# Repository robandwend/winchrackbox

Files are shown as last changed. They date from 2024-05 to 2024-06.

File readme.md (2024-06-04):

# WinchRack-Box V1.1 (WRB)
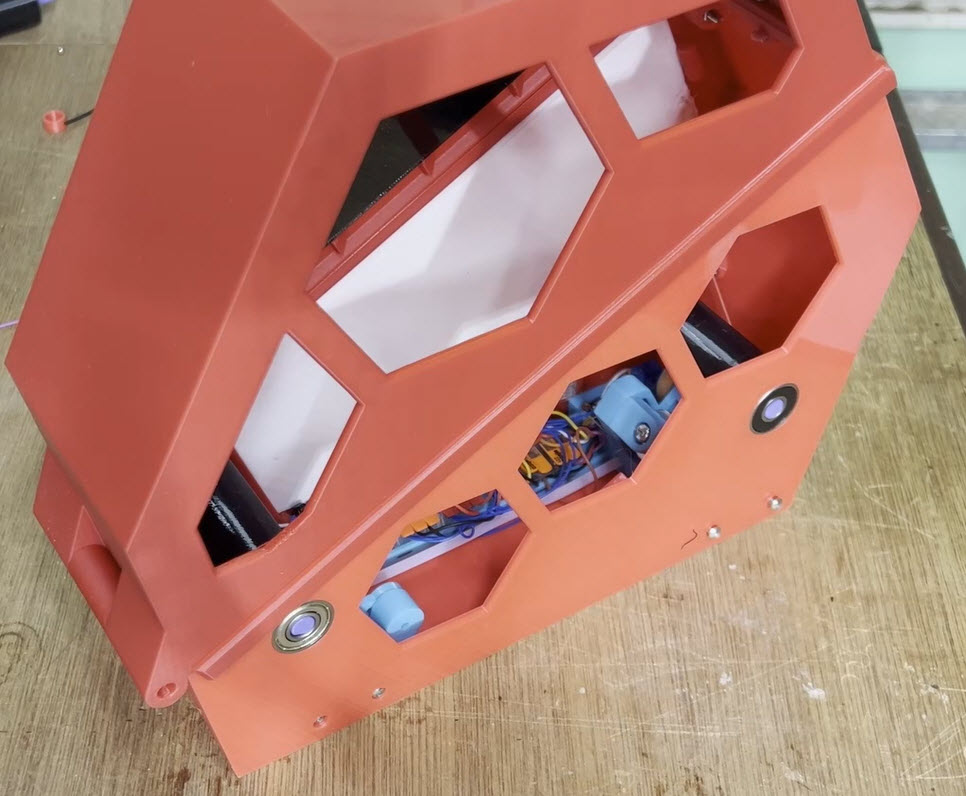
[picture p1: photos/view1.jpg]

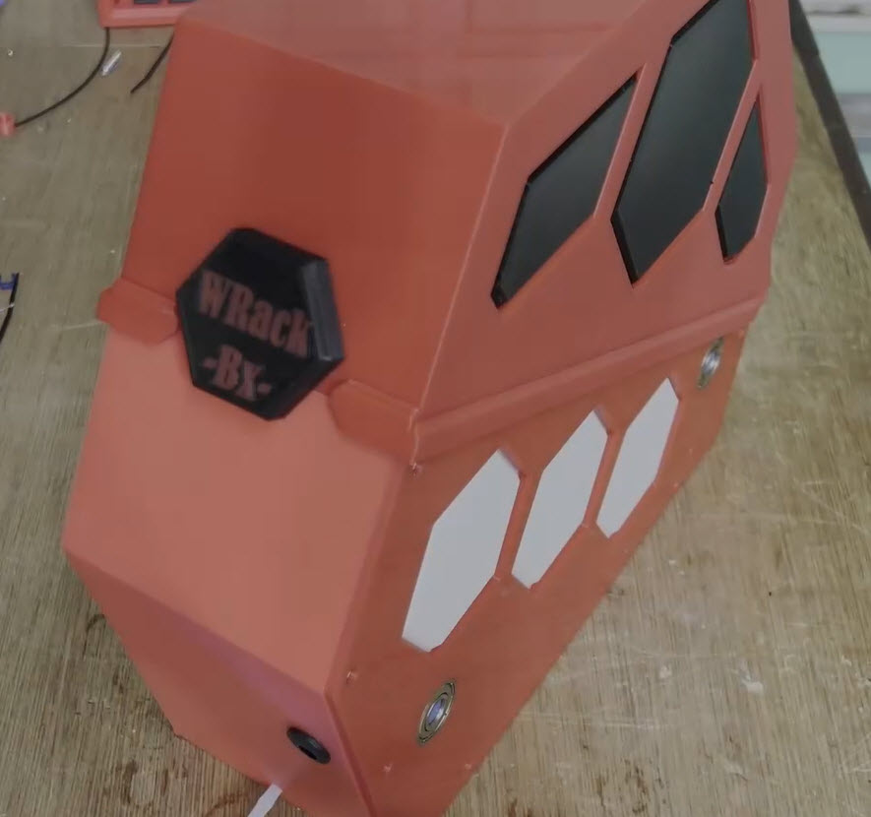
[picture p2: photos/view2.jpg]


## About

Multi filament printers such as ERCF & MMU require some way to store the filament that is retracted during a filament swap.
Various 'buffer' implementations exist for this purpose, however they occupy much space, and make loading / unloading filament more difficult.

The AMS implementation is much neater, rewinding the filament automatically back onto the spool.

This box design allows the spool to be neatly stored, with no need for 'buffers' when used in filament swappers.

The rewind mechanism inside the box is based on this original design by 'Mr Goodman' [LINK TO ORIGINAL WINCHRACK](https://github.com/pure100kim/WinchRack_Type2/tree/main). Although I did made a number of small changes to this design (see [MY CHANGES](https://www.printables.com/model/840978-winchrack_type2-filament-rewinder-for-ercf) ) which I would recommend for the WRB.

The mechanism now has both rollers motor driven to improve the functioning with light (near empty) filament rolls.

The BOM below however is a full component list for the box and mechanism.

Total cost of building a WRB excluding plastics should be less than $17US (plus any shipping costs).

## Youtube intro video

https://youtu.be/9757P2IB9eM

## Printables

https://www.printables.com/model/897767-winchrack-box

## BOM 

Wago 5pin x 2

- Opto endstop x 1 (https://www.aliexpress.com/item/1005005304758202.html)
- n20 gear motor 300 rpm 5v ~ 6v x 1 (https://www.aliexpress.com/item/32910935772.html)
- Solenoid 5v/3kg x 2 (https://www.aliexpress.com/item/32575060483.html)
- mosfet switch 1ch x 1 (https://www.aliexpress.com/item/1005006165294338.html)
- 608zz Bearings x 4 (https://www.aliexpress.com/item/1005005321486587.html)
- 623zz Bearings x 8 (https://www.aliexpress.com/item/1005005480256021.html)
- silicon ring x 1 (https://www.aliexpress.com/item/1005005445878990.html)
- PTFE tube 3x4 or 2x4 (https://www.aliexpress.com/item/1005001408141263.html)
- m3 insert nut (OD 5mm, L 4mm)
- m3 bolts (get a selection pack if you've not already got one)
- m2 self tapping screw 8~10mm x 4
- 6mm collet for 4mm PTFE Tube x 1 (https://www.aliexpress.com/item/4001119588533.html)
- D2F Micro switch (https://www.aliexpress.com/item/1005004693669754.html)
- 4mm Bearing ball (https://www.aliexpress.com/item/1005003377385833.html) (Or these can be taken from inside a 608zz bearing)
- 12V 3A DC Power Connector (https://www.aliexpress.com/item/1005005610836339.html)
- Assorted wego style connectors (https://www.aliexpress.com/item/1005007090402568.html)
- 5V power supply (plugged for your country)

## HOLE VERSION

NOTE: A version of the top hat is available with an additional hex hole in the top (handy if they are all stacked next to each other). 

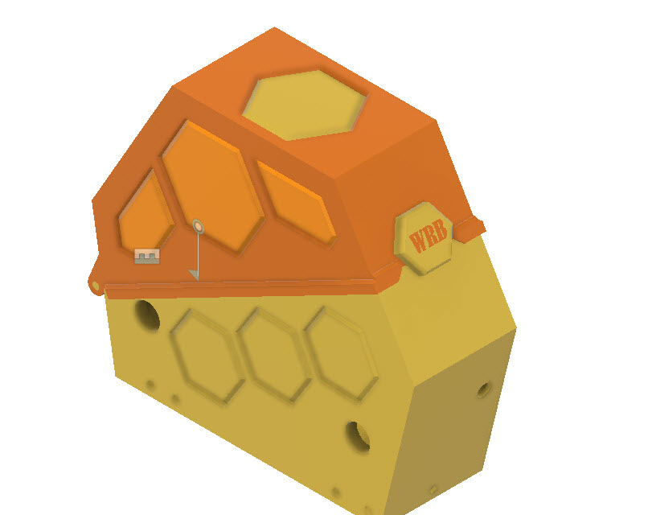
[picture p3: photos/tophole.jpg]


## PRINTING

I've printed all parts in both PLA and PETG and haven't had any problems with either.

### Size

The largest component is the base box, which requires a bedsize of 256x256. I printed on an X1C and a Voron2.4.

### Supports

- The bufferbase_mount (support under the solenoid mount). 

- The box-top as indicated below:

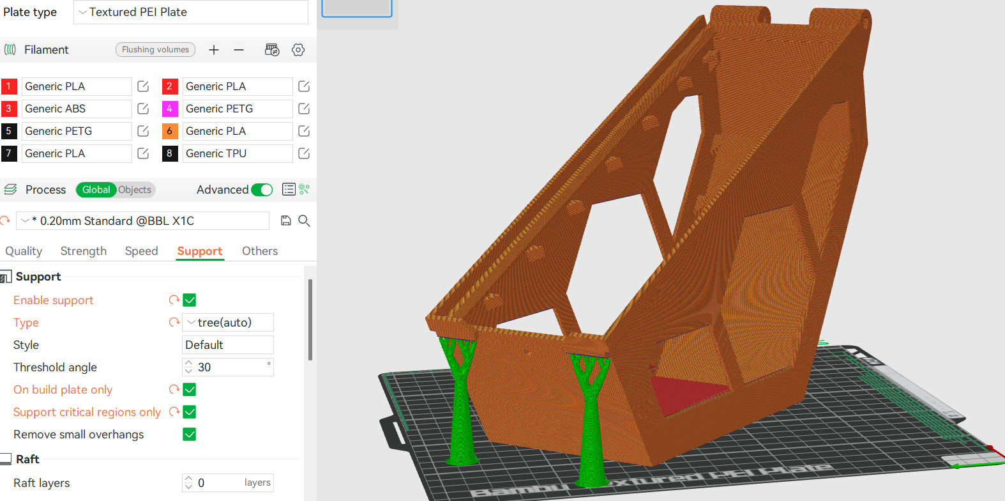
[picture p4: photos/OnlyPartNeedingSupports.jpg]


### Sensor key colour

The opticalsensorkey should be printed in a dark colour to avoid light affecting the optical sensor.

### Rollers

I suggest printing the rollers in TPU to increase friction.

### Sizing

If you find the rollers are not fully connecting to the drive wheels when rewinding, you may wish to reprint the rollers slightly scaled in circumference (say 1mm). I found I needed to do this with one brand of TPU due to shrinkage during printing.

### Knob

The knob is provided as an stl with two bodies, which can be split in the slicer to print the text in a different colour. If the text is not required, then don't split the stl.

Alternatively the knob-no-text stl can be printed, this has the text indented into the knob (ie a single colour print with the text indented).

## BUILD GUIDE

Let the fun begin.

A number of part will need heatset inserts, I'll highlight these as we go.

### Prefer 12Volts?

This is currently a 5Volt build. However by replacing the motors with 12Volt ones, every other component will then work on 12V if preferred.

### Use the right base plate

My suggestion is to build the mechanism onto the right base plate, and get the electronics working before fully assembling the box. I've used wego style connectors to simplify much of the connections. These also allow easy changes to motor directions etc if needed. The wego boxes should snap into place as indicated.

### Insert panels

The hexagonal holes in the box frame are filled with the four panels. Alternatively they can be replaced by 3mm thick clear sheeting cut to size (print a panel as a cutting guide). The panel click into place - however you may want to place a bead of CA glue around their edges to strengthen and reduce air flow.

If you have printed the top with a additional hex hole on its top, then the additional top panel will also be needed (or a clear 3mm perspex cut to size). Note that this panel is a very tight fit, and may require the edges trimmed slightly to fit.

### Drive mechanism

The drive mechanism consists of two separate units, the front and the rear. Both have a drive motor, the rear also has the filament movement sensor.

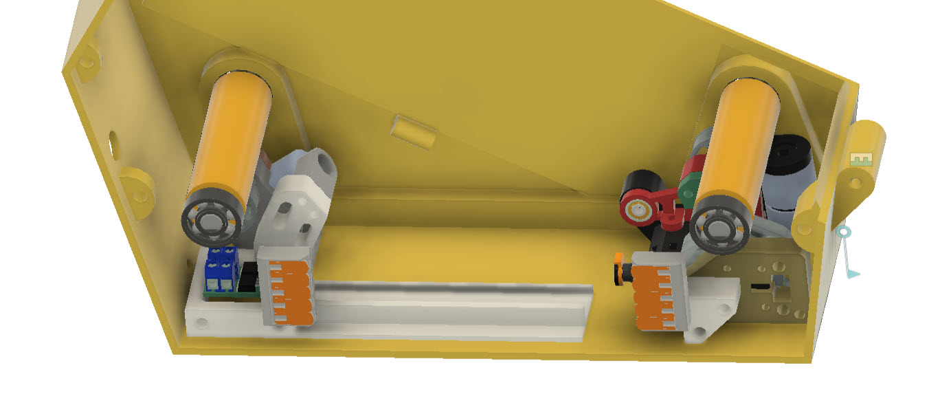
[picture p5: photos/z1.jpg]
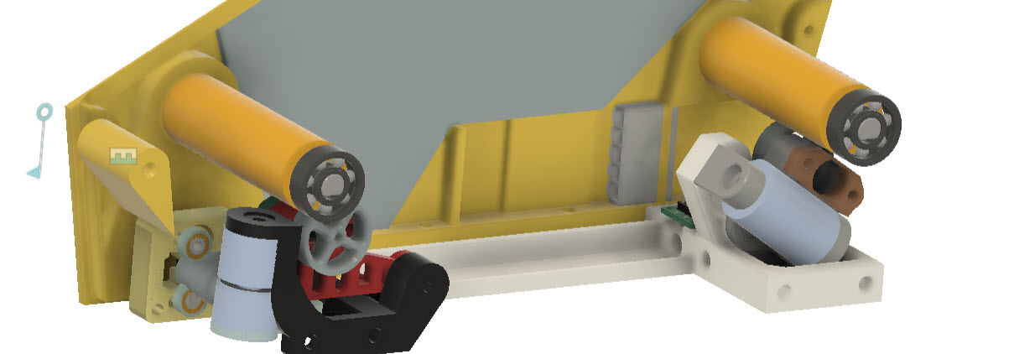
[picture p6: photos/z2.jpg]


## FRONT ASSEMBLY

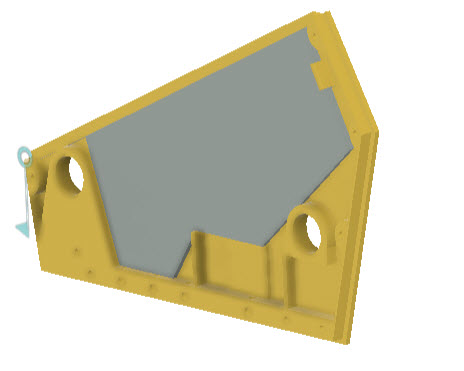
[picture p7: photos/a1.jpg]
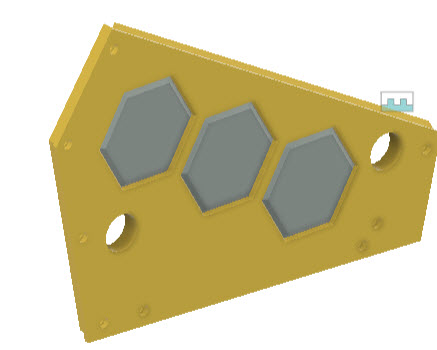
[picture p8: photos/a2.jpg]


- Insert the 608 bearings into the left and right bodies.
- Clip in two 5-point wego connectors
- Clip in the right panel (you can leave out for later if you prefer, this is removable even when completed.)
- Select all the printed parts for the front-assembly.

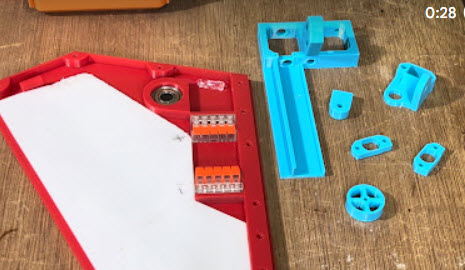
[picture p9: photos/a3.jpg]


- Insert heatset inserts into the locations indicated below

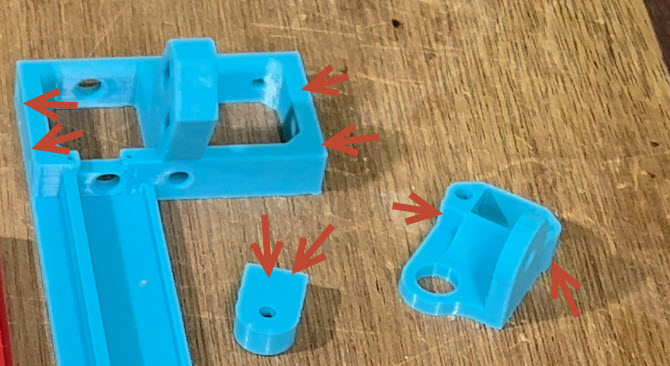
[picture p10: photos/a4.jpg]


- Put the small rubber band around the drive wheel. I find using a small allen key helps lever the band into place.
- Push a small bearing into the AcceleratorMount.
- Assemble the motor into AcceleratorMount and mount cover, and push on the drive wheel.
  - Note that the rear motormount has a small cut-away area that the front one does not have.
  - The wheel must align to the notch on the motor shaft. The fit can be very tight - fortunately the motors can take a surprising amount of pressure.
- Solder a length of wire to the motor (its not clear which is +ve/-ve so later we will test the direction).
  - I always used longer wire leads than needed to ensure I could cut to length later.

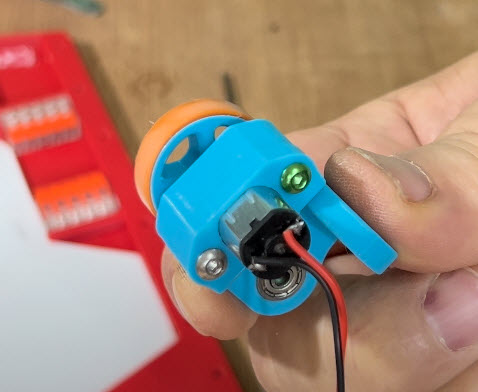
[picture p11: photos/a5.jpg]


- The accelerator assembly will then pivot on the front-base-accel-pedal-mount using the inserted bearing. Screw an m3 bold through the bearing into the pedal-mount.
  - Note that the assembly should move freely as indicated.

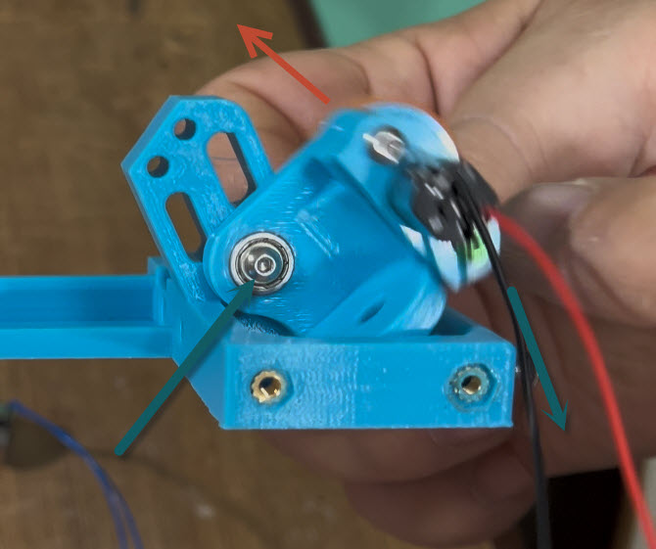
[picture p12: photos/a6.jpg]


Insert a screw into the rear of the mount as shown below. This screw can be used to restrict how far the assembly drops (we only needs about 2mm gap between the solenoids once fitted).

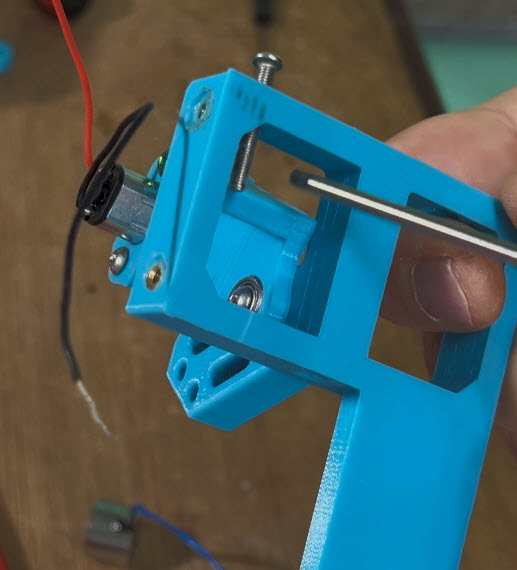
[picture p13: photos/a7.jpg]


- Attach a solenoid as shown using an m4 bolt (sometimes the bolt is supplied with the solenoid - sometimes its not).
- Route the four wires through the base, using the 2nd hole (the first/middle hole is for ptfe tube for the filament to route through).

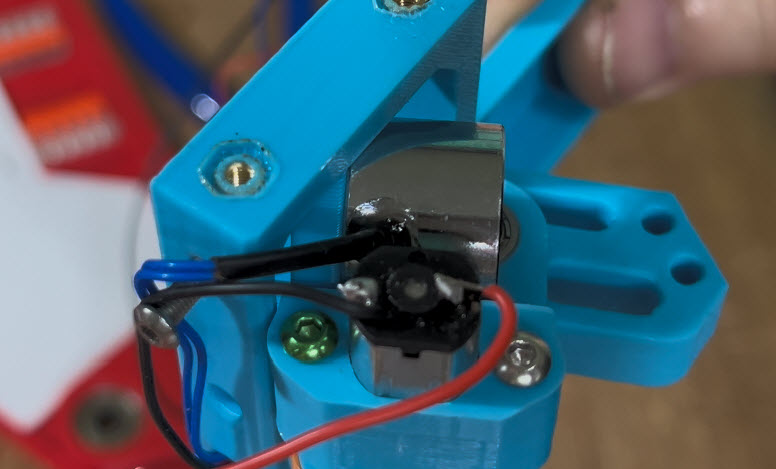
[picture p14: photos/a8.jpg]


- Attach 2nd solenoid to the AccelPedalMagSol

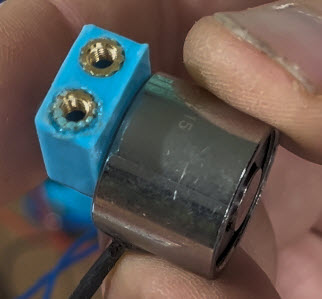
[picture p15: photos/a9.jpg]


- Use two screws to attach this as shown, routing the wires through the slot.

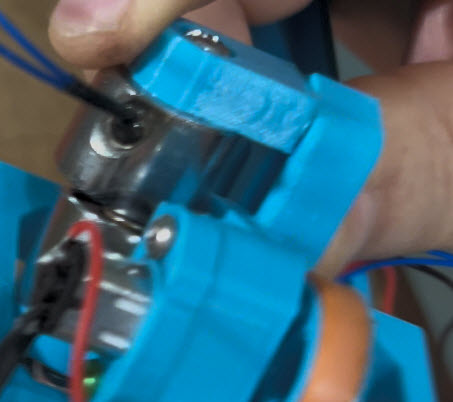
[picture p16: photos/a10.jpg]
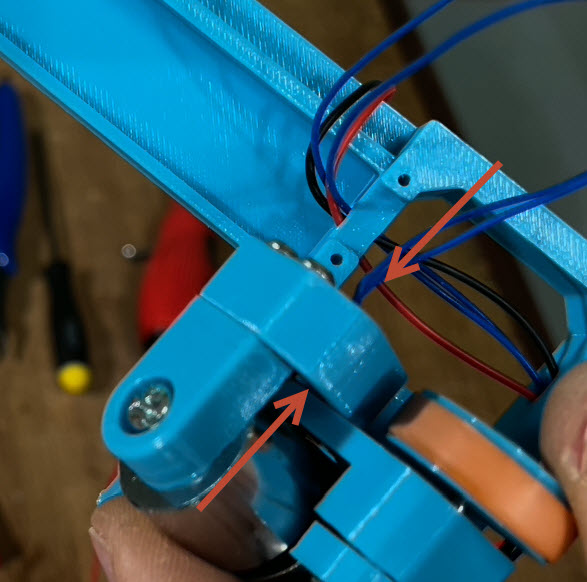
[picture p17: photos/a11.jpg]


- Adjust the solenoids to be flat to each other
  - The screws holding the solenoids and the AccelPedalMagSol all have a very slight movement. Slacken the screws, physically hold the solenoids together, and re-tighten.
  - At this point we are looking for a movement of about 2mm between the solenoids. When held flat on the table, the solenoids should fall apart 2mm easily. The gap can be reduced using the screw inserted at the rear of the base.
  - If the movement is not very easy, then loosen the bolt holding the pivot bearing.
  - Also ensure that the wire routing is not affecting the movement.

<video width="320" height="240" controls>
  <source src="videos/ss.mov" type="video/mp4">
</video>

[You Tube Copy](https://youtu.be/2NZAOF3inoc)

- Take the mosfet switch and connect a length of wire to one of the trigger connections (it doesn't matter which one).
  - Leave a good length of wire as this will route through to the microswitch on the rear assembly.

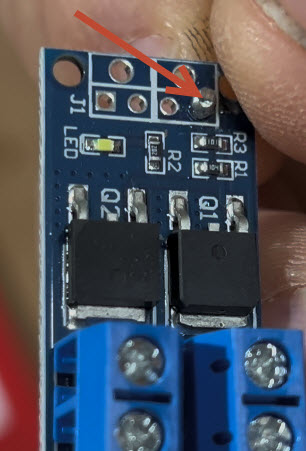
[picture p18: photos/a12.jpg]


- Screw in four lengths of cable to the mosfet as shown. We do this now because once attached to the base, it becomes difficult to a access. Again leave plenty of length on the cables so we can trim to size later.

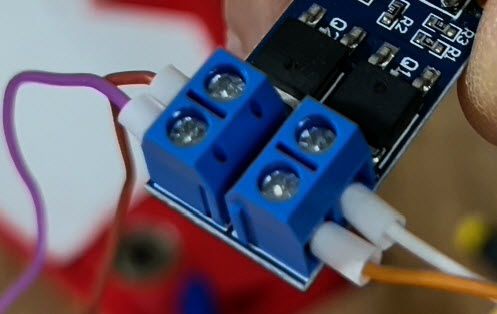
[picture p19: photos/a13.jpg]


- Attach the mosfet to the base as shown using two m2 self-tapping screws.

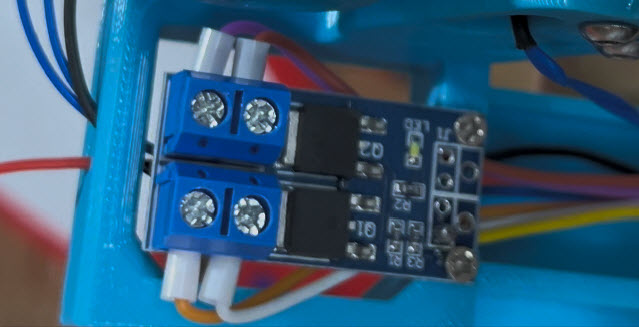
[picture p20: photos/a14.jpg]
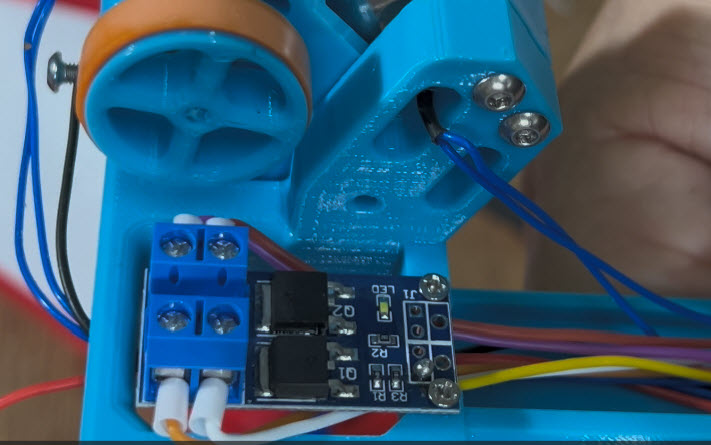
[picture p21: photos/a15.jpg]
 

- Attach the assembly to the side panel using two m3 screws.

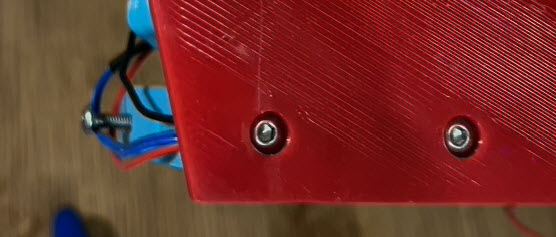
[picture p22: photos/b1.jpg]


### Wiring

For reference here's the wiring design for the original Type2 winchrack, the only change is to add a second motor and set of solenoids. I've added a few extra Wago blocks to aid connections.

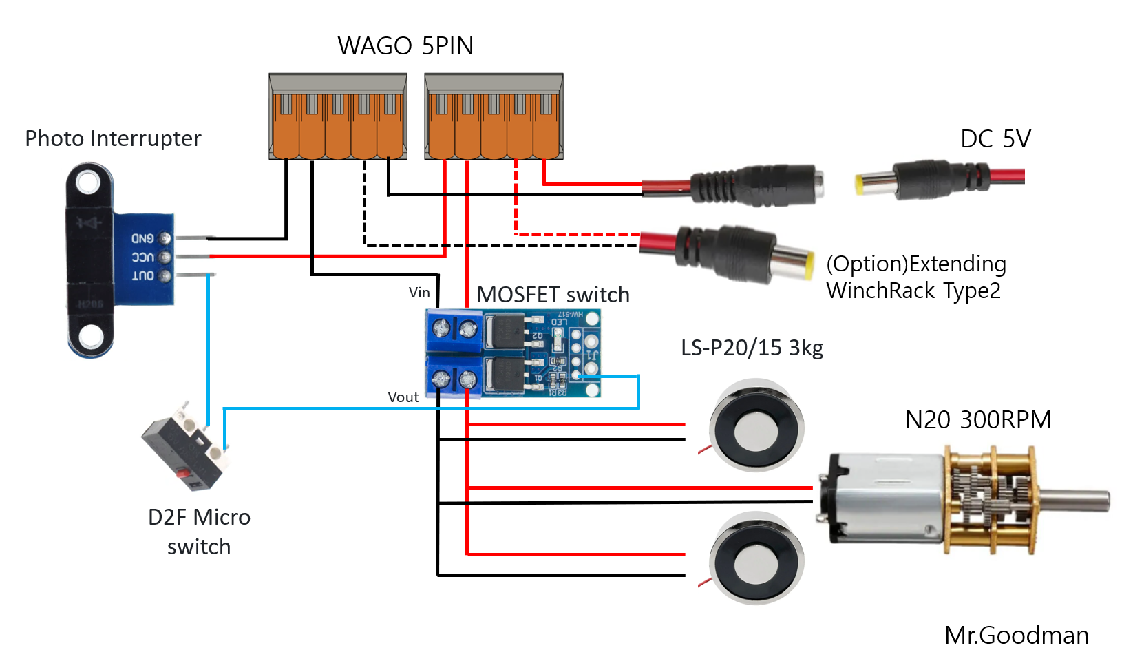
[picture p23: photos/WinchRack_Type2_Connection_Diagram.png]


### Wiring the front assembly

<video width="320" height="240" controls>
  <source src="vidoes/fa.mov" type="video/mp4">
</video>

[You Tube Copy](https://youtu.be/1QWAKU8oQXM)

The front assembly has three devices that need to be driven - The motor, and the two solenoids.

We will use the two wego connectors to create a +ve and -ve terminal, use a marker to indicate which is going to be used for which.

#### Motor connection
  - Use a 5 Volt supply to test the direction of the motor. You want the motor to turn so the top moves to the front of the unit. Shorten and insert the +ve/-ve of the motor into the correct wego blocks.

#### Solenoid connection. 
  - Here we need to determine the correct leads to connect together.
  - Twist one lead from each of the solenoids to one from the other solenoid. Do the same with the 2nd lead from each. 
  - Connect 5V to see if the solenoids snap together (move them by hand to check the distance isn't too far.)
  - If they snap together, then we have the correct pairing, if not, then swap over the pairings and retry.
  - Having established which wires go together, plug the twisted wires into the +ve and -ve wego blocks. (Which is +/-ve doesn't matter),

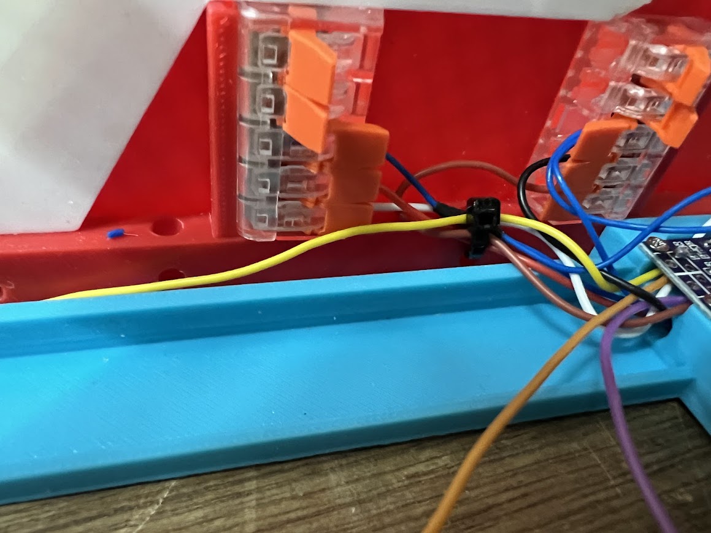
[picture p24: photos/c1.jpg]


- Power in connector block
  - Add to 3-block wego connectors onto the right of the rail on the base of the front assembly. 
  - These will be the main 5V input power points of the build. (The 5-unit blocks are only energised when the motors are to run).
  - Mark the 3-block wego's with +ve and -ve
  - Run a wire from each block back through the hole in the front assembly (where most of the wires are running) - this will later be connected to the power source using a 12v connector. I'd suggest using red/black wires to indicate +/-ve.

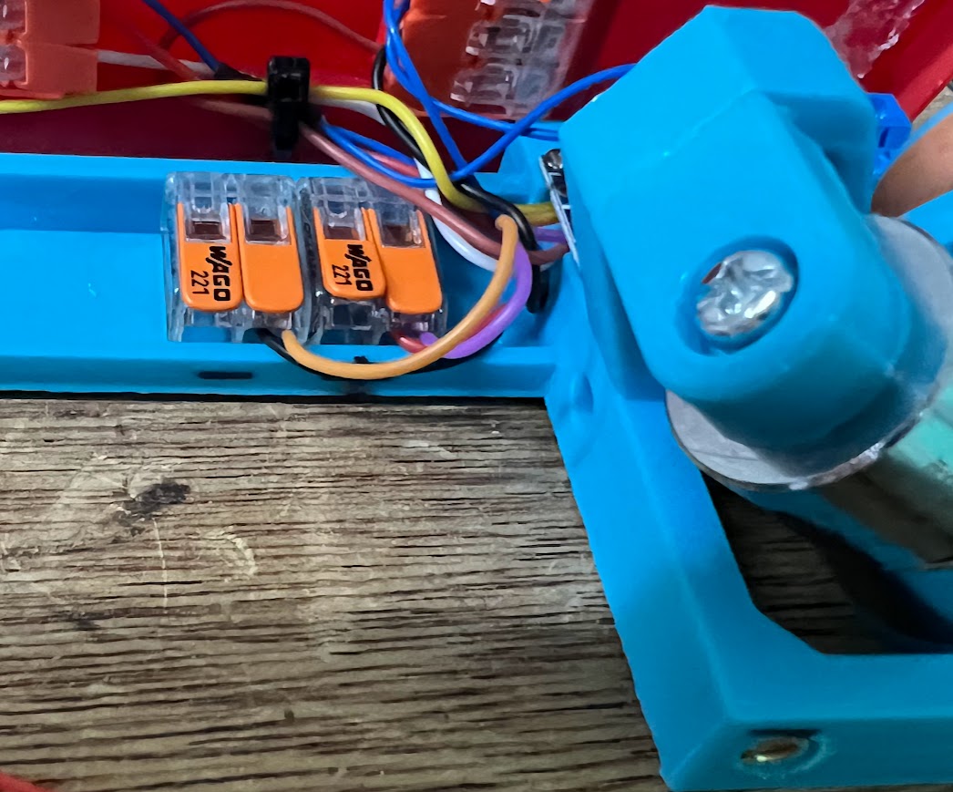
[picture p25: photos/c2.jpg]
 (Note: I've used a 2-connector as this was all I had at hand)
  
- Mosfet connection.
  - Plug the +/-ve IN wires from the mosfet into the +/- 3-block wego connectors (ie the power in wego just added).
  - Plug the +/-ve OUT wires from the mosfet into the +/- 5-block wego connectors (ie to power the motor and the solenoids).
  
At this point the only wire not connected (other than the main 5v power input) is the wire going to the mosfet trigger. This will be connected later.

Note the zip tie connection points down the side to aid tidying the wires.

## REAR Assembly

Gather the parts needed for the rear assembly

- Add heatset inserts as indicated.

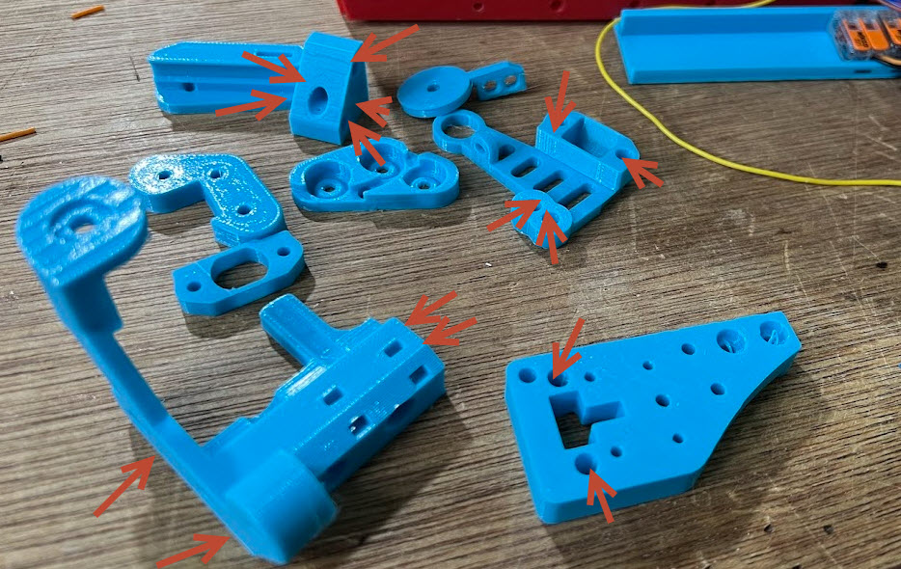
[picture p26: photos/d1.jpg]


### BufferRail Assembly

- Add four bearings as shown. Connected with m3 screws. Ensure they are tight, but free to move.

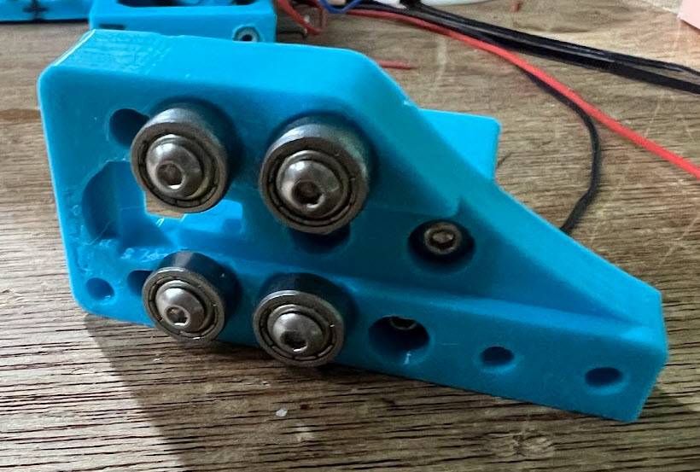
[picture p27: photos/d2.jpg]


- Attach the SensorDetection_sensor_basemount to the bufferrail. Not that this has a hole for later routing of wires.

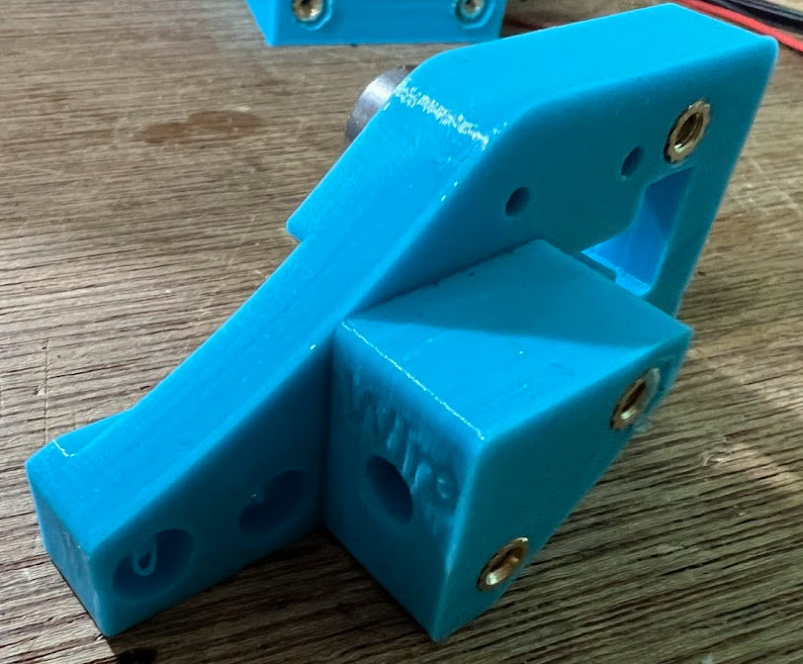
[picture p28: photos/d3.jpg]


- Push a bearing into the AccelPedalMag
- Attach the BaseSolJoint to the AccelPedalMag
- Screw an M3 screw in as shown. This can be used later to restrict the movement of the pedal.
- Solder two wires to the motor (leave sufficient length to trim later).
- Insert the motor into the pedal as shown.

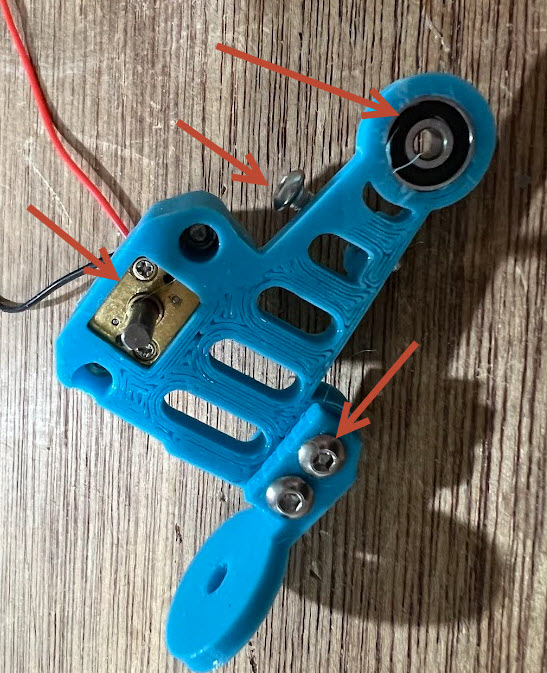
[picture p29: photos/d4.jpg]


- Attach the motor using the motor-mount. Note that the rear motor-mount has a small cut-away area that the front one does not have.

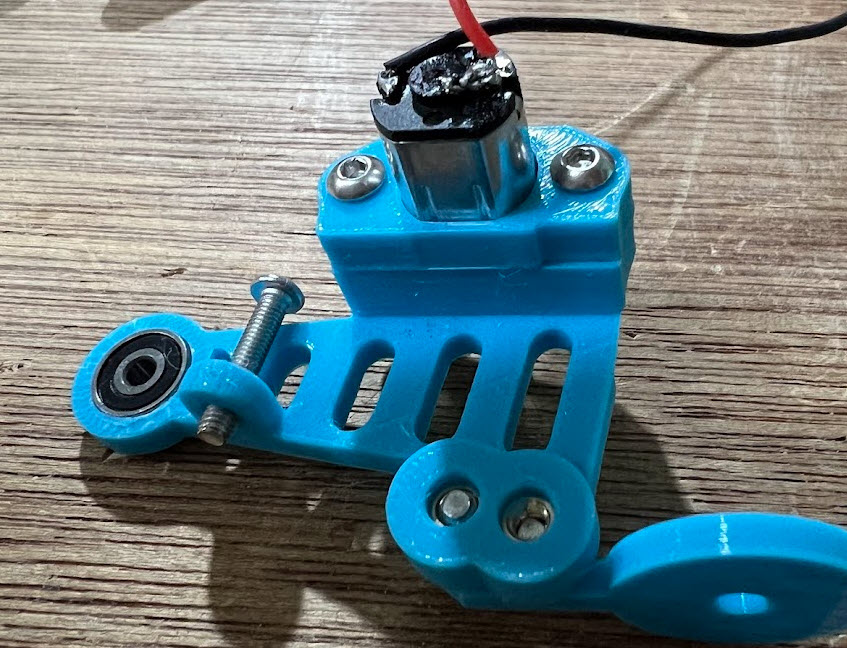
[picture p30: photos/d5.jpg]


- Again place a band over/around the wheel.
- Attach the wheel to the motor, like the front wheel, this is a tight fit.

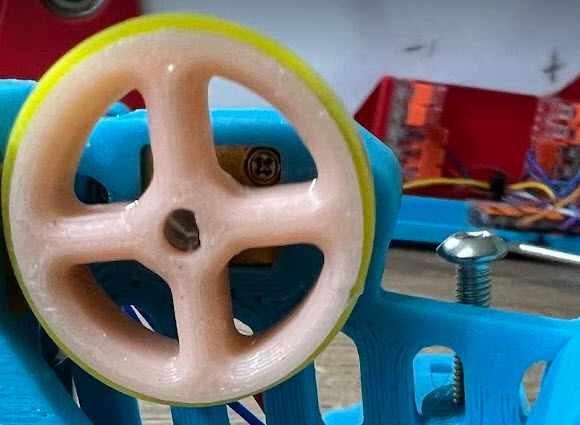
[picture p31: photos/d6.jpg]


- Attach the AccelPedalMag to the Bufferbase_mount with a single screw through the bearing (as done with the front). You can now see how the screw fitted earlier can be used to limit travel.
    - Ensure the pedal moves freely.
    - Ensure your heatset insert isn't as poorly fitted as the one in this photo :-)

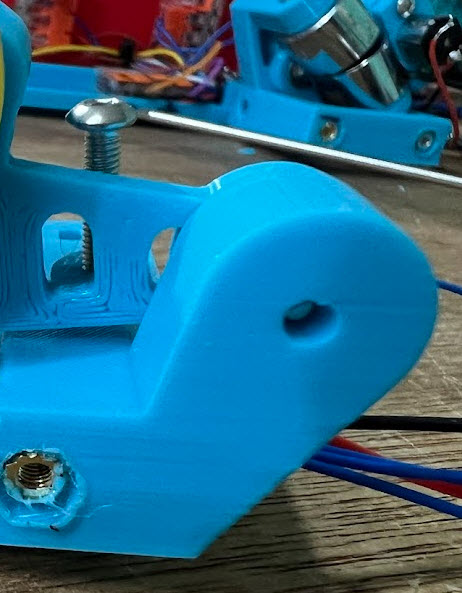
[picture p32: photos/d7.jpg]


### Solenoids

- Attach the solenoids as show.
    - Again use the slight free-play when the screws are loose to ensure a good closed fit between the two solenoids.
    - You only need a 1 or 2mm gap between the open solenoids.

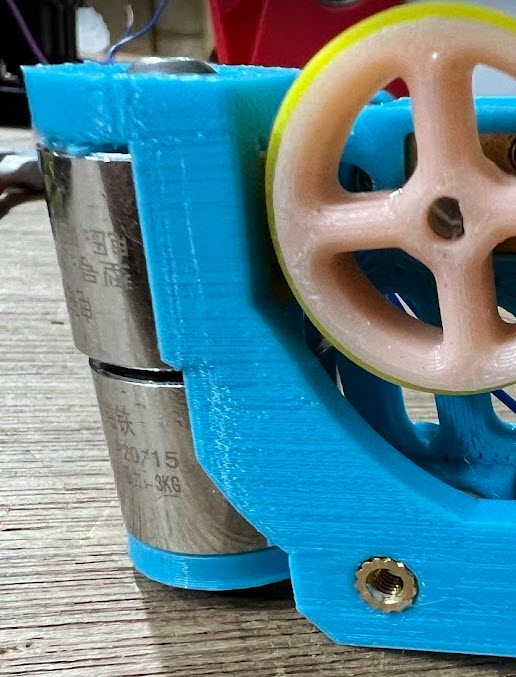
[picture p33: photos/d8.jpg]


- Route the wires through the hole as shown

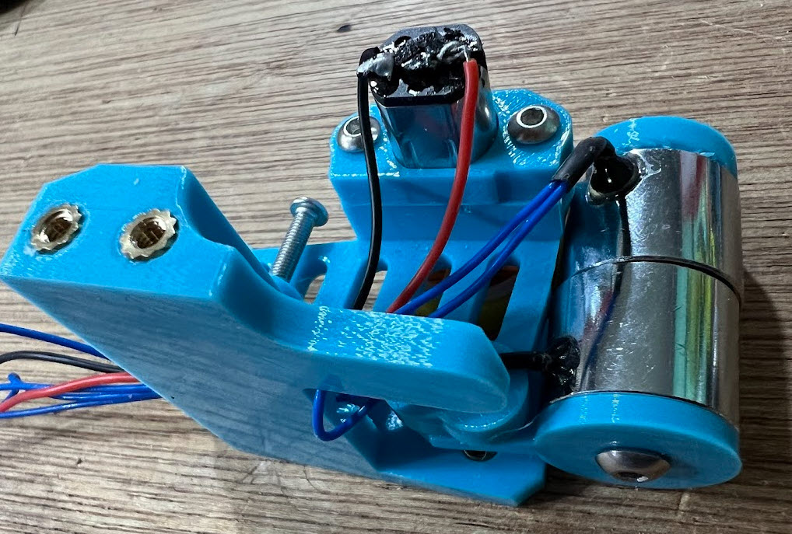
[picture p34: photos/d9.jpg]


### Sensor Roller Assembly

The sensor roller is use to detect filament movement. The filament routes through it between three bearings, the bearings cause a small amount of friction on the filament - thus making the sensor move.

- This image shows the three components of the roller, in order of stacking with the bearings in position.
- Assemble as shown and screw together with three m3 screws.

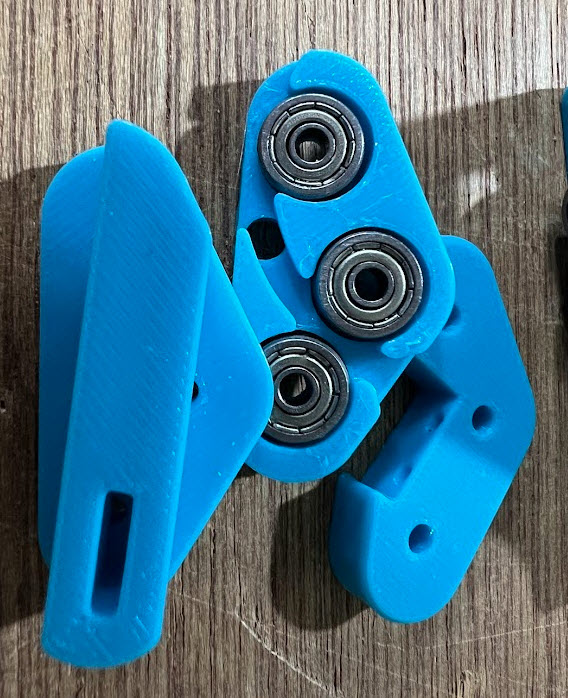
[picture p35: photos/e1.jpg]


- Place a ball-bearing in to the hole where the microswitch will fit.
- Screw in the microswitch with 2.5 self tapping screws.
- Place the roller into the bufferrail as shown.

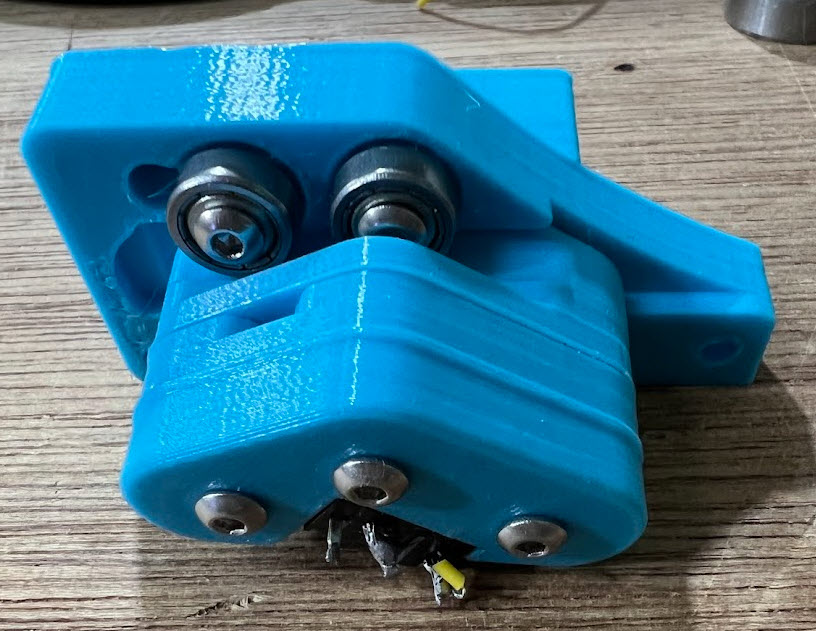
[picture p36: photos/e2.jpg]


- Rotate the bufferrail, so you can see the open 'T' where the opto-endstop will fit. Align the sensorRoller so you can see the slot for the OpticalSensorKey. 
- Insert the OpticalSensorKey. I would suggest printing this in black to aid the opto-endstop working.

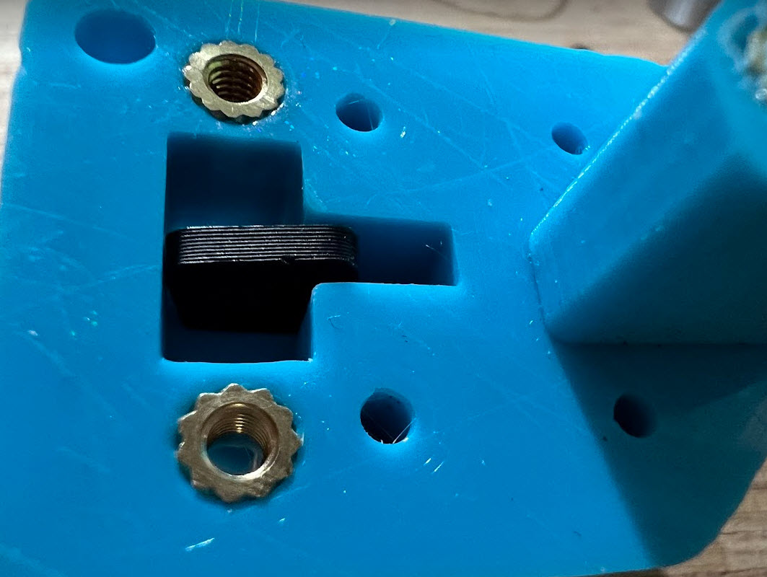
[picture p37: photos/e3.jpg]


- Attach the opto-endstop.

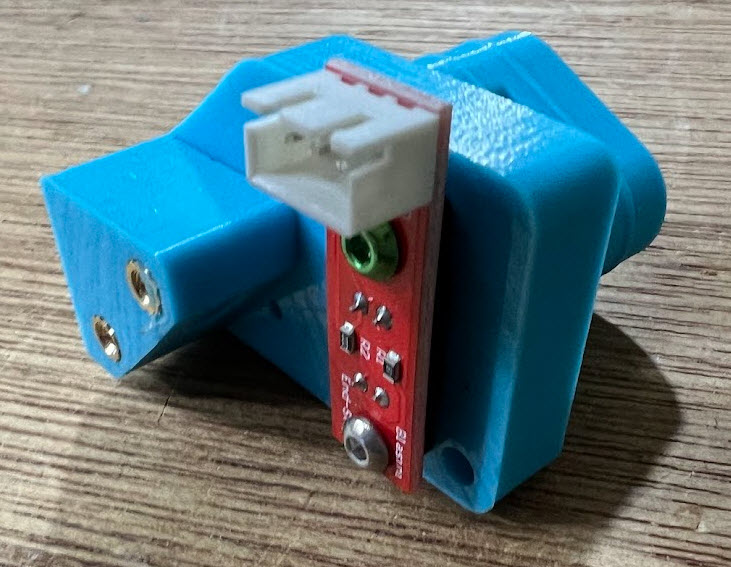
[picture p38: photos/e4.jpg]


- Route the centre wire from the endstop as shown, and connect to the microswitch.

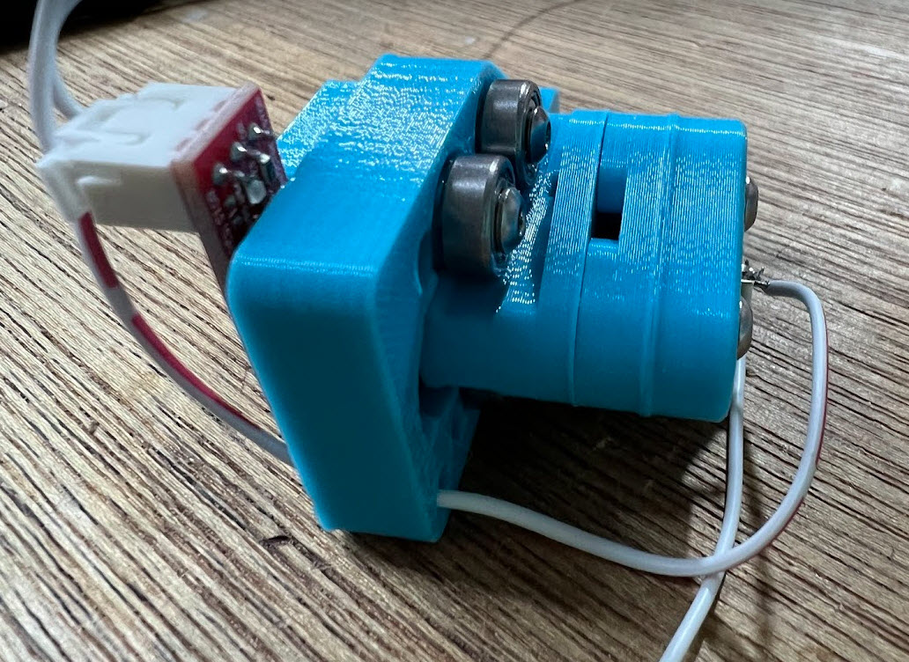
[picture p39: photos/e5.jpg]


- Attach the motor assembly to the bufferrail.
- Attach this assembly to the rear plate.
- Attach the +ve and -ve from the opto-endstop to the +/- on the main 5V power blocks. (RED ARROW)
- Attach the other end of the microswitch to the existing lead connected to the mosfet-switch trigger. (GREEN ARROW)
    - In this image, I've connected this using an additional connector-block.

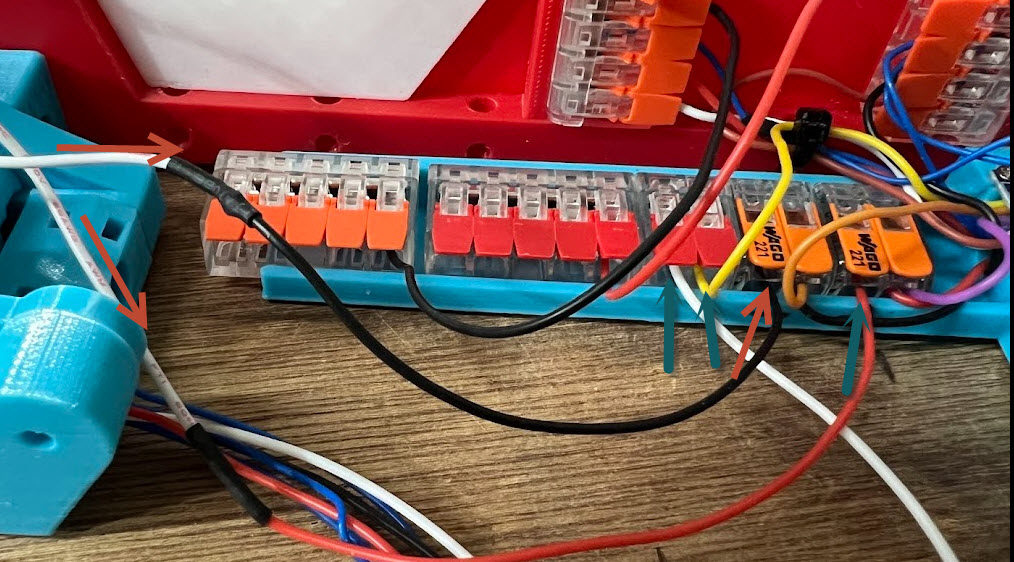
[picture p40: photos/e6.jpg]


### Wiring the rear

- Only the motor and two solenoids remain to be wired. Like the front motor/solenoids these need connecting to the +/-ve of the two 5-Blocks. To get more connection points we will add two more 5-blocks, and connect them with short wires to the original 5-blocks.



- As done for the front motor we need to work out the +ve / -ve using a 5V supply.
- Plug the motor into the new 5-block +/-ve.
- As done for the front solenoids we need to match up the correct wires (try one way and then the other).
- Plug the solenoids into the new 5-block +/-ve.

### Testing

- Place a small length of filament through the sensor roller, pulling / pushing this filament should start the motors.
- Use a 5V supply connected to the main 5v power input (yet to be attached to the plug socket) to test the solenoids and the motors turn.
- If the motors turn in the wrong direction (as in the video) then you can easily swap the +/-ve connectors.

<video width="320" height="240" controls>
  <source src="videos/wt.mov" type="video/mp4">
</video>

[You Tube Copy](https://youtu.be/CsUi9PYC_X0)

### Collet

- Push the 6mm collet into the bufferbase-mount.



### Final assembly

#### Plug connection

- Insert the plug-socket into the main body
- Connect this to the main 5v input wires.



#### Rollers

- Attach the two rollers, with the shaft and tpu-rollerpipes with 2.5mm spacers on either side.

 <img 

#### Body build

- Join the two body parts. There are several screw points around the body.
  - This may need some fiddling to get all the parts to align correctly. Ensure no wires are caught and the 2.5mm spacers don't fall out.

  

#### Hinge mechanism

- The centre hinge will need two heat inserts before attaching as shown

 

#### PTFE

- Thread a length of PTFE (length ill depend on your needs) as shown.

 

### Top

- The top can be attached at the hinge with two screws, and two screws for the knob mechanism.

 

### Knob

- The knob is attached with one screw through the hole in the top.
- A second screw in the base protrudes and allows the knob to lock the box.

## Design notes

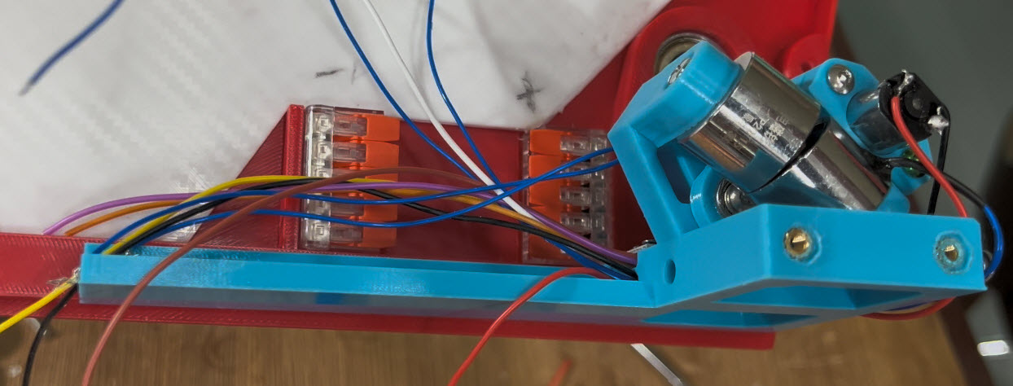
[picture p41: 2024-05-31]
photos/b2.jpg

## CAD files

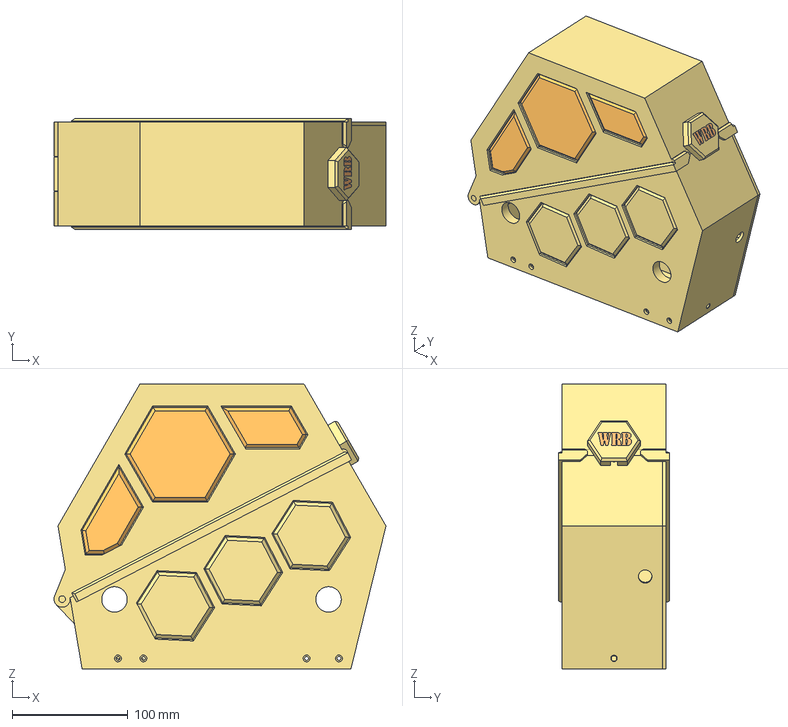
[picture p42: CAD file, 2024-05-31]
CAD/WinchRack_Box_2Drive v2.3.step
286.9 x 96.0 x 246.0 mm
knob
Body-left-panel
Pin (Placeholder)
Body-Right-Panel
Top
Hinge
TopInsertPanels
BufferRail_New

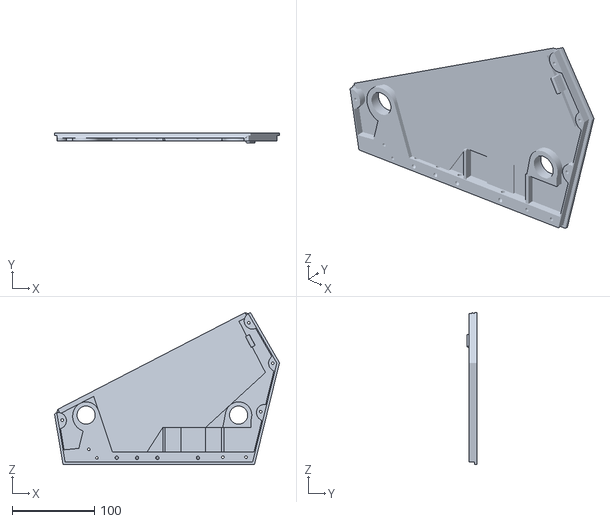
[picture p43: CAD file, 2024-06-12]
STLs/Enclosure/Body-Right.stl
273.0 x 12.5 x 184.5

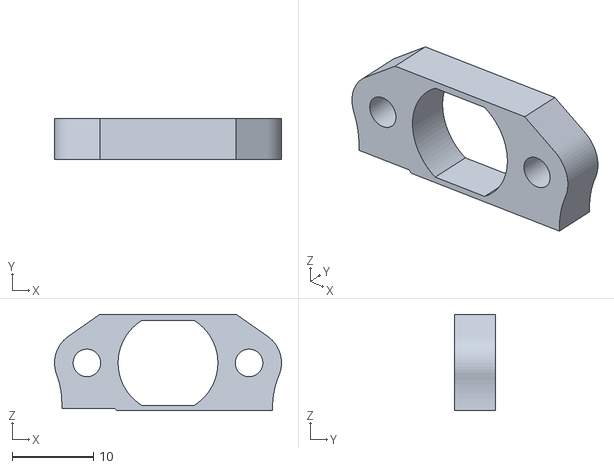
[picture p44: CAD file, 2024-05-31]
STLs/WinchRackV2(Original)_stls/AccelMotor/AccelPedal_Motor_holder.stl
28.0 x 5.00 x 11.9

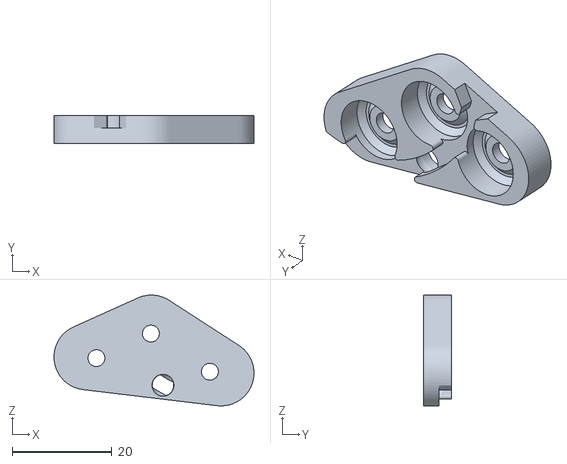
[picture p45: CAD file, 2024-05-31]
STLs/WinchRackV2(Original)_stls/SensorDetection/SensorDetection_middle_Narrow.stl
40.2 x 5.61 x 22.3

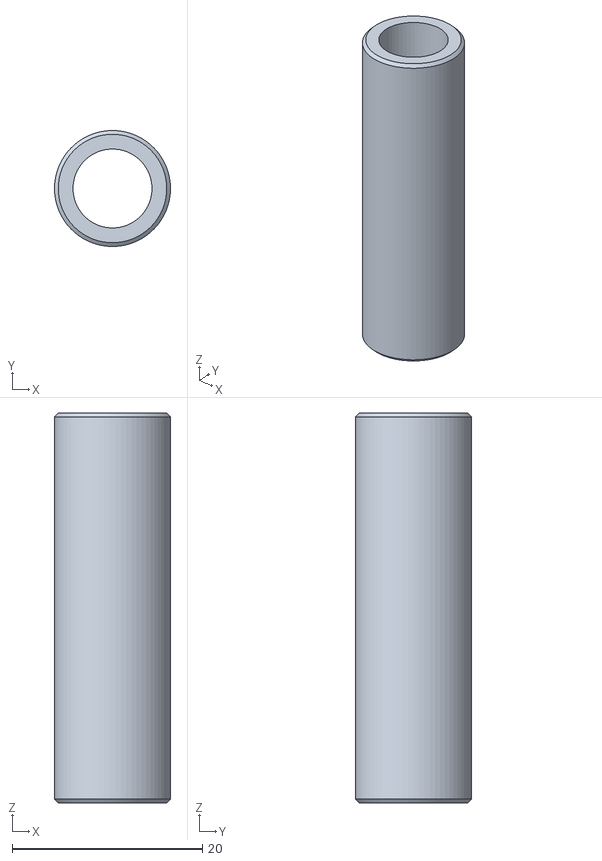
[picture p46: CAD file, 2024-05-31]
STLs/WinchRackV2(Original)_stls/SpoolBase/41mm_pipe.stl
12.2 x 12.2 x 41.0

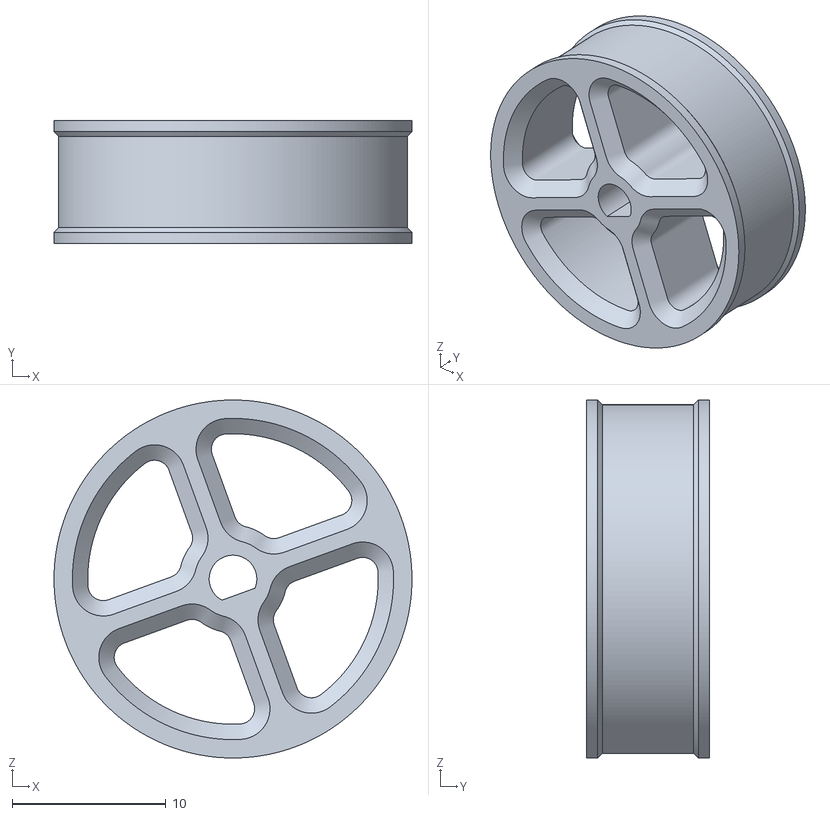
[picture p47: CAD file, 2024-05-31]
STLs/WRB Front/Front_Roller.stl
23.3 x 8.00 x 23.3

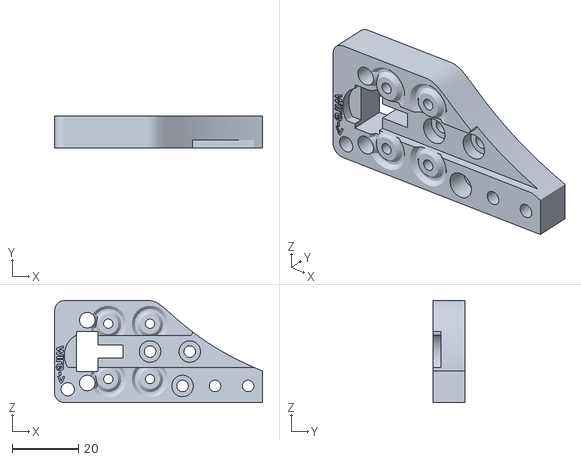
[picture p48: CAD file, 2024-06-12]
STLs/WRB Rear/wrb_buffer_rail(as per bom).stl
62.9 x 9.58 x 30.9

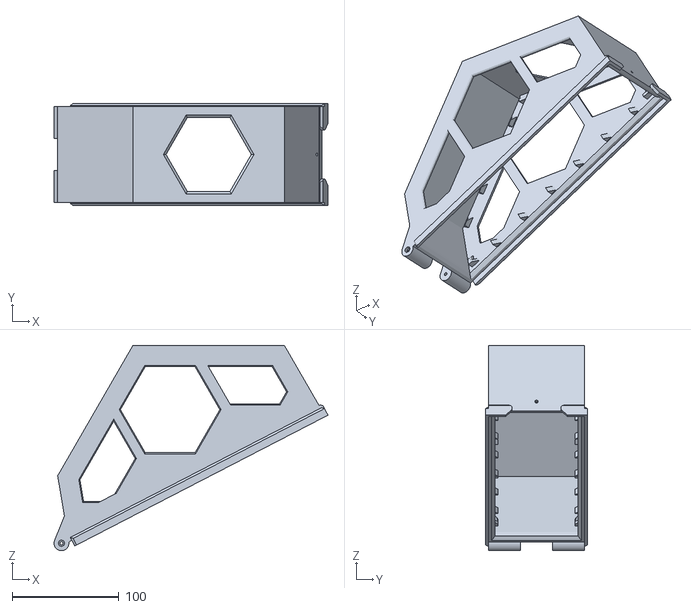
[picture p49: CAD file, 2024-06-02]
STLs/Enclosure/Top (Option With hole).stl
257.2 x 96.0 x 192.8

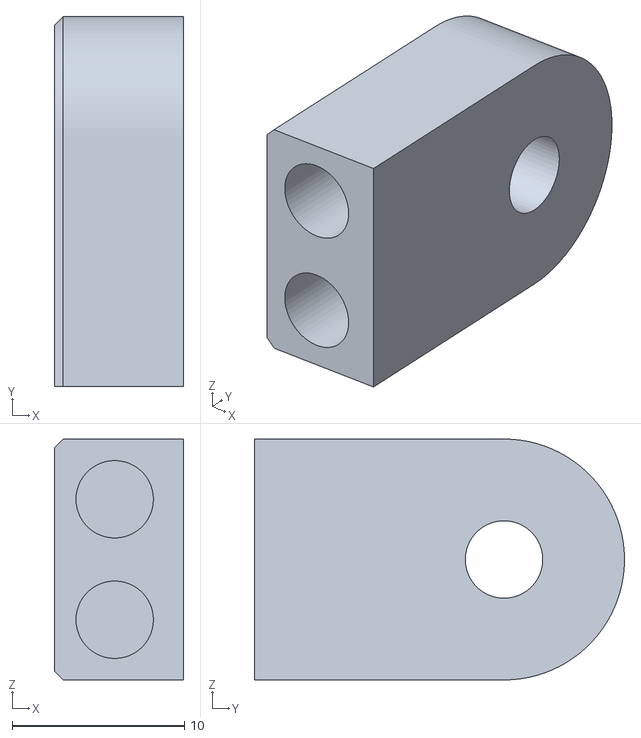
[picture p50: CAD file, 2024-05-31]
STLs/WinchRackV2(Original)_stls/AccelMotor/AccelPedal_mag_holder.stl
7.50 x 21.5 x 14.0

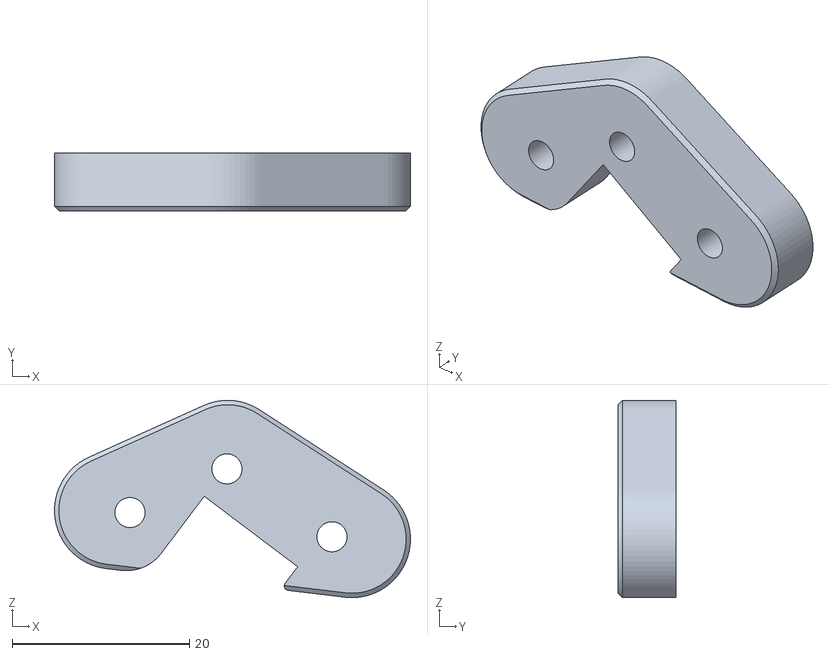
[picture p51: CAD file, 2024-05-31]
STLs/WinchRackV2(Original)_stls/SensorDetection/SensorDetection_Switch_mount.stl
40.2 x 6.50 x 22.3

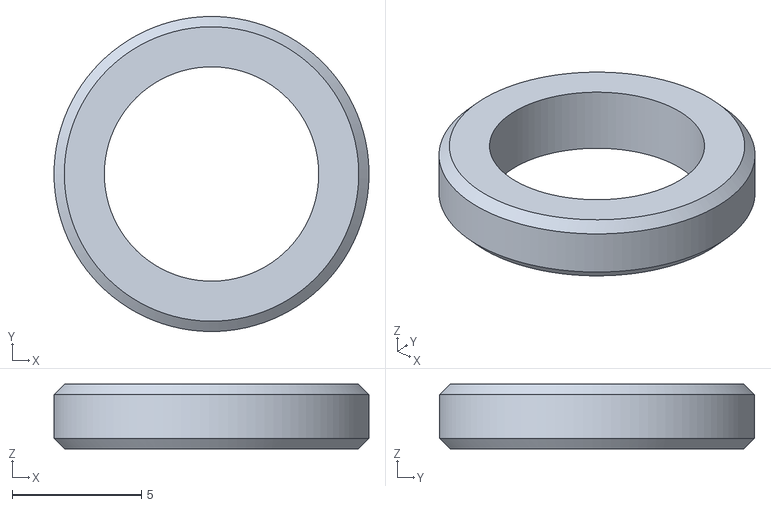
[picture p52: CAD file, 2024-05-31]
STLs/WinchRackV2(Original)_stls/SpoolBase/2.5mm_space x 4.stl
12.2 x 12.2 x 2.50

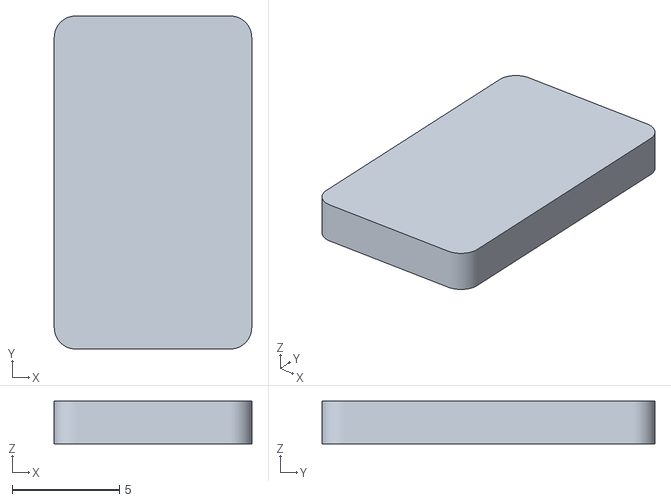
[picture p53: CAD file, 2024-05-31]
STLs/WRB Rear/OpticsensenceKey(BLK).stl
9.20 x 15.5 x 2.00

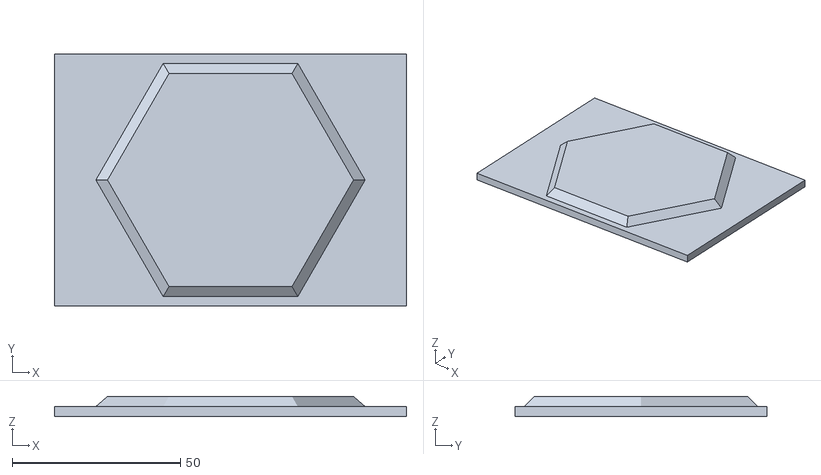
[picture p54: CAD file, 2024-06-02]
STLs/Enclosure/Top top-hole-insert.stl
104.6 x 74.8 x 6.00

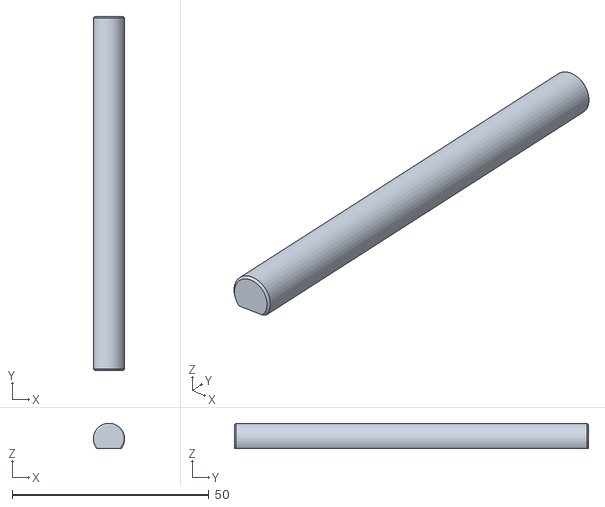
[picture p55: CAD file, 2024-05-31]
STLs/WinchRackV2(Original)_stls/SpoolBase/Shaft2_Flat.stl
7.94 x 90.0 x 6.46

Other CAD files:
STLs/WRB Front/AccelPedalMagSol.stl
STLs/WinchRackV2(Original)_stls/AccelMotor/AccelPedal_Roller.stl
STLs/WinchRackV2(Original)_stls/SensorDetection/SensorDetection_Photo_senseKey.stl
STLs/WRB Front/Motor_Mount.stl
STLs/Enclosure/2.5mm space X 4.stl
STLs/Enclosure/Body-Right-Panel.stl
STLs/Enclosure/Body-left-panel.stl
STLs/Enclosure/Bottom-Left.stl
STLs/Enclosure/Hinge.stl
STLs/Enclosure/Knob-text.stl
STLs/Enclosure/RollerPipe(tpu) x2.stl
STLs/Enclosure/Shaft X 2.stl
STLs/Enclosure/Top.stl
STLs/Enclosure/TopInsertPanel - L.stl
STLs/Enclosure/TopInsertPanel - R.stl
STLs/Enclosure/knob(split after loading).stl
STLs/Enclosure/knob-no-text.stl
STLs/WRB Front/AccelPedalMag.stl
STLs/WRB Front/Front Base_Accel_Pedal_Mount.stl
STLs/WRB Rear/AccelPedalMag.stl
STLs/WRB Rear/BaseSolJoint.stl
STLs/WRB Rear/BufferBase_mount.stl
STLs/WRB Rear/Buffer_Rail(Option2).stl
STLs/WRB Rear/Motor_Mount.stl
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

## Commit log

2024-05-31 Here we go...
    [2.5mm space X 4.stl, 2.5mm_space x 4.stl, 41mm_pipe.stl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]
2024-06-02 Panels missed
    [Body-Right-Panel.stl, Body-left-panel.stl]
2024-06-02 Added option to have hole in top of box
    [Top (Option With hole).stl, Top top-hole-insert.stl]
2024-06-02 Top hole photo added
2024-06-04 2nd roller stl added
    [Front_Roller.stl]
2024-06-12 Added both buffer rail versions
    [Buffer_Rail(Option2).stl, wrb_buffer_rail(as per bom).stl]
2024-06-12 Missing a recess in side
    [Body-Right.stl]
